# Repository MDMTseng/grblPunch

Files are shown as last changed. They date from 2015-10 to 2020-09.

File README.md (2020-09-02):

# Patch for GRBL project supporting the creation of punch machine for barrel organs.

The original GRBL Project is located at : [http://github.com/grbl/grbl](http://github.com/grbl/grbl) this project is a fork specialized in punch machines as below. It has a X and Y axis plus a punch command for punching holes in the barrel organ book.

This GRBL project has a gui for handling the punch plan, and grbl control using a PC, Mac or Linux. please see the associated software website : [www.barrel-organ-discovery.org](http://www.barrel-organ-discovery.org/site/krunch.html)

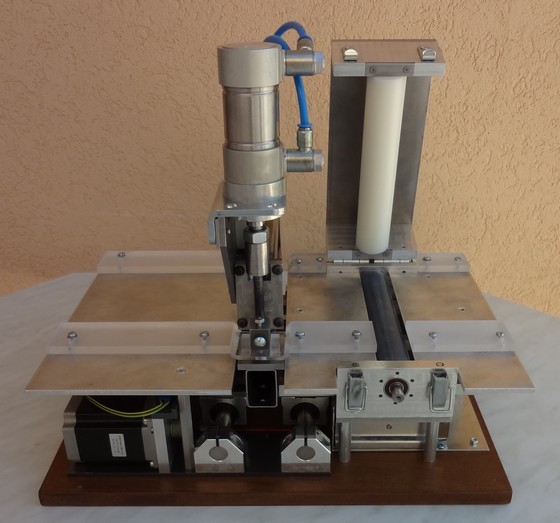
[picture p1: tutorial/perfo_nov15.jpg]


Punch machine designed and constructed by Jean Pierre Rosset.

## Introduction

This patch add a new <b>M100 GCode</b> command designed for punching machines. This new punching M100 command handle the punch cycle. This command permit to wire the punch actuators and sensor and use them in a GCode program

The punch cycle introducted is the following

- activate the punch down actuator
- wait for the punch to be on bottom (wait the activation of the punchdown sensor)
- activate the punch up actuator
- wait for the punch to be up

at least you must have two sensors for the punch positions (up and down). the activation of the up actuator is optional as some punch actuator, once desactivated, move up the punch.

Only Arduino Uno CPU is supported yet in this version.

## Grbl introducted modifications

In the adjustment of grbl software :

- The spindle is disconnected, and the pins are reuse for punching
- The D12 and D13 are now used for handling the actuators for the punch
- The A4 and A5 pins for detecting the state of the punch (up or down)

All other pins are remained the same.

## Arduino Uno connexions used by this patch

## Schematic View

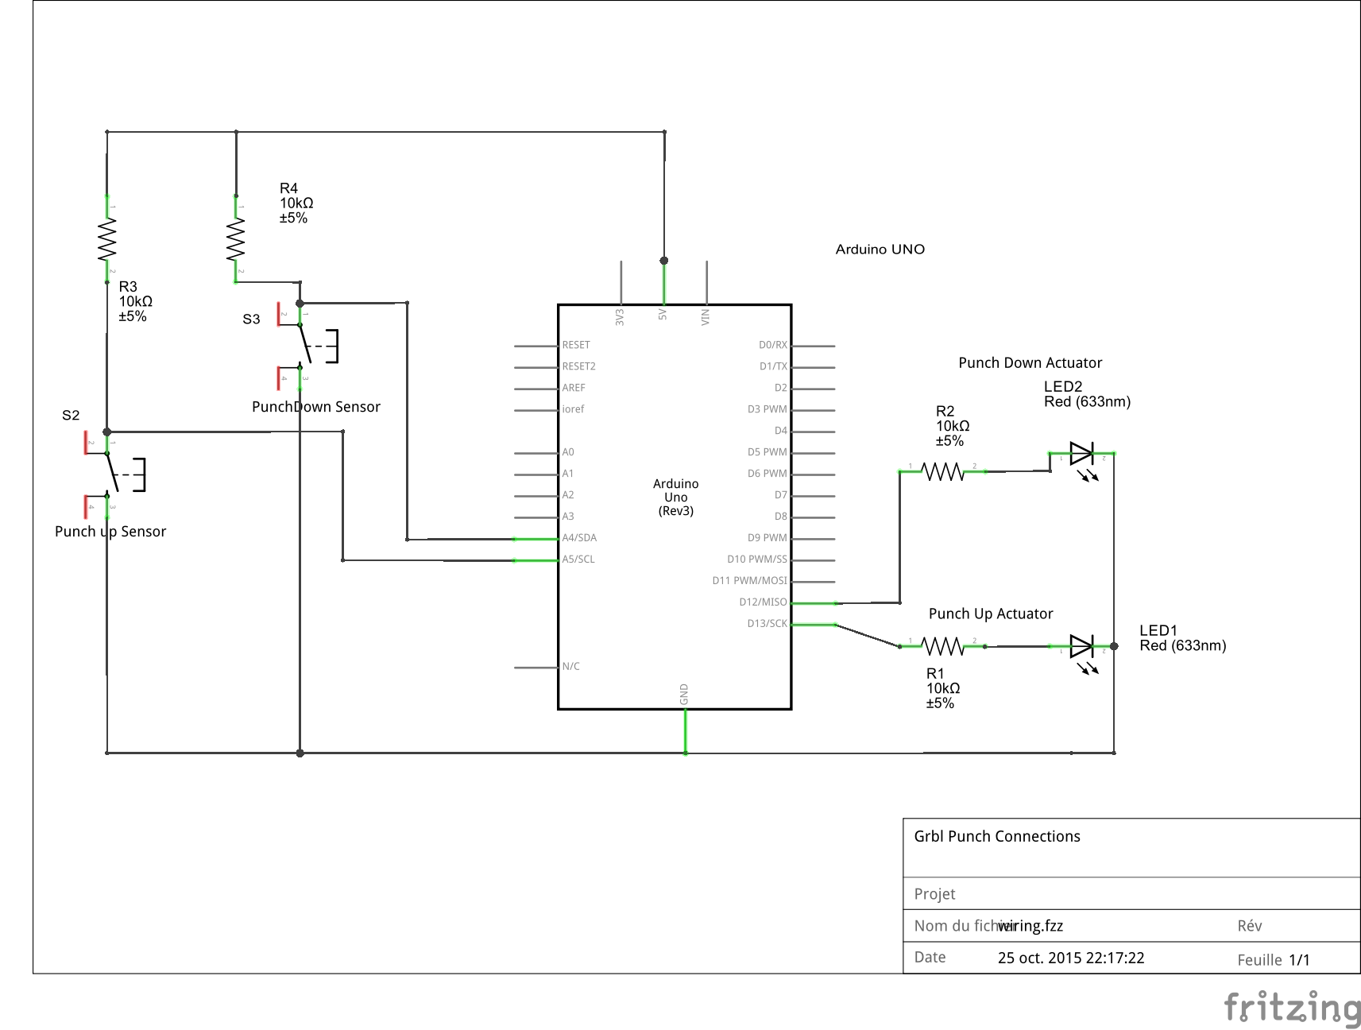
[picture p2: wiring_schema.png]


## Prototype view

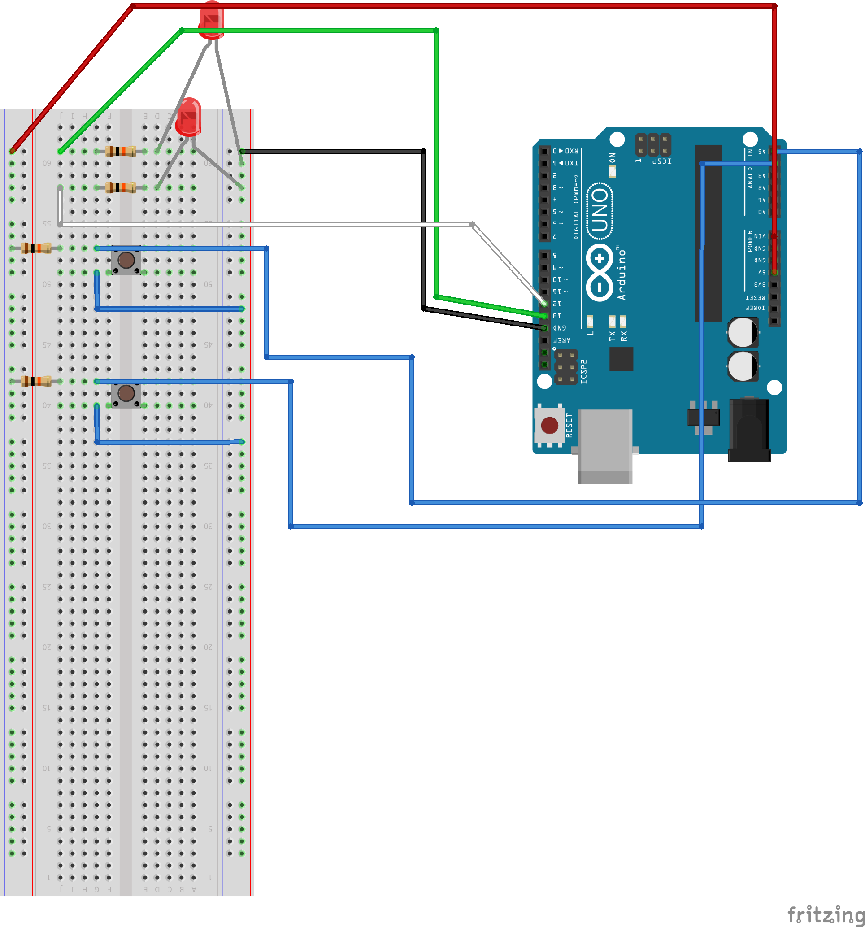
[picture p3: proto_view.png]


## Video demonstrating the new GCode Command

[https://www.youtube.com/watch?v=Sks70Pnujw8](https://www.youtube.com/watch?v=Sks70Pnujw8)

# Install the Grbl Punch software on Arduino Uno

the Easiest way to install the software is to use the XLoader software 

you can download this software at this url [http://russemotto.com/xloader/](http://russemotto.com/xloader/)

Launch XLoader

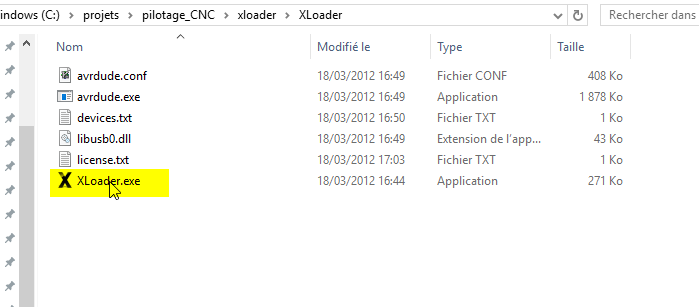
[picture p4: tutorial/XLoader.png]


Upload the grblPunch.hex file, 

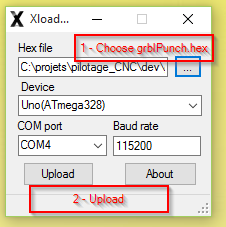
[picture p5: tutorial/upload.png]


**Warning : please download the hole project as a zip file, and take the grblPunch.hex file from it. Using internet Explorer to save the file as a text file can corrupt the file.**

That's all

You can then use the universal code sender to connect and configure the elements.

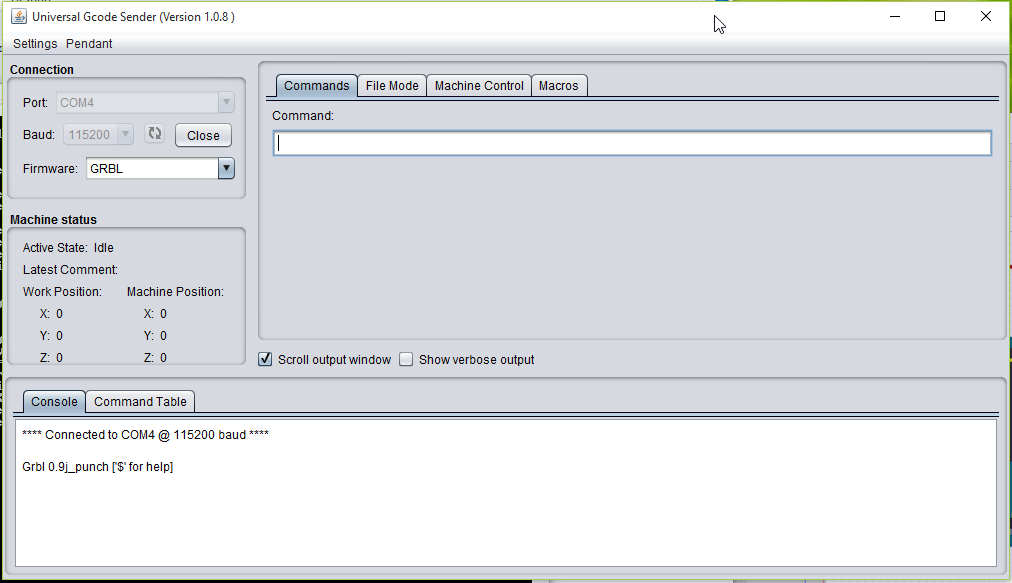
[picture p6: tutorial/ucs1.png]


## Settings 

Additional settings are introducted in this version of grbl, $30, $31, $32, $33 for adjusting the behaviour of the punch cycle, depending on the actuator and sensors used.

	>>>> $30=0 (punch actuator down invert, bool)
	>>>> $31=0 (punch actuator up invert, bool)
	>>>> $32=1 (punch sensor down invert, bool)
	>>>> $33=1 (punch sensor up invert, bool)

the $32 and $33 settings permit to invert the detection of the punch position. 

<table>
<tr>
	<th>setting</th>
	<th>value</th>
	<th>description</th>
</tr>
<tr>
	<td>$30</td>
	<td>0</td>
	<td><b>The punch down</b> actuator is activated if the PIN is at <b>"5v"</b></td>
</tr>
<tr>
	<td>$30</td>
	<td>1</td>
	<td><b>The punch down</b> actuator is activated if the PIN is at <b>"0v"</b></td>
</tr>
<tr>
	<td>$31</td>
	<td>0</td>
	<td><b>The punch up</b> actuator is activated if the PIN is at <b>"5v"</b></td>
</tr>
<tr>
	<td>$31</td>
	<td>1</td>
	<td><b>The punch up</b> actuator is activated if the PIN is at <b>"0v"</b></td>
</tr>
<tr>
	<td>$32</td>
	<td>0</td>
	<td><b>The punch down</b> is detected down if the sensor is <b>"0v"</b></td>
</tr>
<tr>
	<td>$32</td>
	<td>1</td>
	<td><b>The punch down</b> is detected down if the sensor is <b>"5v"</b></td>
</tr>
<tr>
	<td>$33</td>
	<td>0</td>
	<td><b>The punch up</b> is detected up if the sensor is <b>"0v"</b></td>
</tr>
<tr>
	<td>$33</td>
	<td>1</td>
	<td><b>The punch up</b> is detected up if the sensor is <b>"5v"</b></td>
</tr>

</table>

you can view the associated parameters in launching the $$ command

	$$
	$0=10 (step pulse, usec)
	$1=25 (step idle delay, msec)
	$2=0 (step port invert mask:00000000)
	$3=0 (dir port invert mask:00000000)
	$4=0 (step enable invert, bool)
	$5=0 (limit pins invert, bool)
	$6=0 (probe pin invert, bool)
	$10=3 (status report mask:00000011)
	$11=0.010 (junction deviation, mm)
	$12=0.002 (arc tolerance, mm)
	$13=0 (report inches, bool)
	$20=0 (soft limits, bool)
	$21=0 (hard limits, bool)
	$22=0 (homing cycle, bool)
	$23=0 (homing dir invert mask:00000000)
	$24=25.000 (homing feed, mm/min)
	$25=500.000 (homing seek, mm/min)
	$26=250 (homing debounce, msec)
	$27=1.000 (homing pull-off, mm)
	>>>> $30=0 (punch actuator down invert, bool)
	>>>> $31=0 (punch actuator up invert, bool)
	>>>> $32=0 (punch sensor down invert, bool)
	>>>> $33=0 (punch sensor up invert, bool)
	$100=250.000 (x, step/mm)
	$101=250.000 (y, step/mm)
	$102=250.000 (z, step/mm)
	$110=500.000 (x max rate, mm/min)
	$111=500.000 (y max rate, mm/min)
	$112=500.000 (z max rate, mm/min)
	$120=10.000 (x accel, mm/sec^2)
	$121=10.000 (y accel, mm/sec^2)
	$122=10.000 (z accel, mm/sec^2)
	$130=200.000 (x max travel, mm)
	$131=200.000 (y max travel, mm)
	$132=200.000 (z max travel, mm)

you can change a setting value using

	$33=1

## Improvements - RoadMap

<b>2016 - February</b>

- fix sensor detection, additional material has been setted up, we still need 2 sensors for the punch (eliminating the time in the equation)

<b>2015 - November</b>

- <strike>by settings, 
    - able to use a "pull up" logic on the hard limit
    - or use two 0-1 detector on both side of the X axis</strike>

<b>2015 - November</b>

- Validation of the master branch with a real machine

<b>Todo</b>

- Check at startup that the punch is up, before starting (part of the homing cycle checks)

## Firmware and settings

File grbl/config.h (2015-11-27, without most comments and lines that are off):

#define config_h
#include "grbl.h" // For Arduino IDE compatibility.
#define DEFAULTS_GENERIC
#define BAUD_RATE 115200
#define CPU_MAP_ATMEGA328P // Arduino Uno CPU
#define CMD_STATUS_REPORT '?'
#define CMD_FEED_HOLD '!'
#define CMD_CYCLE_START '~'
#define CMD_RESET 0x18 // ctrl-x.
#define CMD_SAFETY_DOOR '@'
#define HOMING_INIT_LOCK // Comment to disable
#define HOMING_CYCLE_0 (1<<X_AXIS)                // REQUIRED: First move Z to clear workspace.
#define N_HOMING_LOCATE_CYCLE 1 // Integer (1-128)
#define HOMING_FORCE_SET_ORIGIN // Uncomment to enable.
#define N_STARTUP_LINE 2 // Integer (1-2)
#define N_DECIMAL_COORDVALUE_INCH 4 // Coordinate or position value in inches
#define N_DECIMAL_COORDVALUE_MM   3 // Coordinate or position value in mm
#define N_DECIMAL_RATEVALUE_INCH  1 // Rate or velocity value in in/min
#define N_DECIMAL_RATEVALUE_MM    0 // Rate or velocity value in mm/min
#define N_DECIMAL_SETTINGVALUE    3 // Decimals for floating point setting values
#define MESSAGE_PROBE_COORDINATES // Enabled by default. Comment to disable.
#define SAFETY_DOOR_SPINDLE_DELAY 4000
#define SAFETY_DOOR_COOLANT_DELAY 1000
#define ACCELERATION_TICKS_PER_SECOND 100
#define ADAPTIVE_MULTI_AXIS_STEP_SMOOTHING  // Default enabled. Comment to disable.
#define TOOL_LENGTH_OFFSET_AXIS Z_AXIS // Default z-axis. Valid values are X_AXIS, Y_AXIS, or Z_AXIS.
#define PUNCH_ACTIVATED
#define MINIMUM_JUNCTION_SPEED 0.0 // (mm/min)
#define MINIMUM_FEED_RATE 1.0 // (mm/min)
#define N_ARC_CORRECTION 12 // Integer (1-255)
#define ARC_ANGULAR_TRAVEL_EPSILON 5E-7 // Float (radians)
#define DWELL_TIME_STEP 50 // Integer (1-255) (milliseconds)
#if defined(USE_SPINDLE_DIR_AS_ENABLE_PIN) && !defined(VARIABLE_SPINDLE)
  #error "USE_SPINDLE_DIR_AS_ENABLE_PIN may only be used with VARIABLE_SPINDLE enabled"
#endif
#if defined(USE_SPINDLE_DIR_AS_ENABLE_PIN) && !defined(CPU_MAP_ATMEGA328P)
  #error "USE_SPINDLE_DIR_AS_ENABLE_PIN may only be used with a 328p processor"
#endif
#if defined(VARIABLE_SPINDLE) && defined(PUNCH_ACTIVATED)
  #error "YOU CAN'T HAVE PUNCH FUNCTIONALITY WITH SPINDLE"
#endif

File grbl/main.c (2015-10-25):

/*
  main.c - An embedded CNC Controller with rs274/ngc (g-code) support
  Part of Grbl
  
  Copyright (c) 2011-2015 Sungeun K. Jeon
  Copyright (c) 2009-2011 Simen Svale Skogsrud
  
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
  You should have received a copy of the GNU General Public License
  along with Grbl.  If not, see <http://www.gnu.org/licenses/>.
*/

#include "grbl.h"


// Declare system global variable structure
system_t sys; 


int main(void)
{
  // Initialize system upon power-up.
  serial_init();   // Setup serial baud rate and interrupts
  settings_init(); // Load Grbl settings from EEPROM
  stepper_init();  // Configure stepper pins and interrupt timers
  system_init();   // Configure pinout pins and pin-change interrupt
  
  memset(&sys, 0, sizeof(sys));  // Clear all system variables
  sys.abort = true;   // Set abort to complete initialization
  sei(); // Enable interrupts

  // Check for power-up and set system alarm if homing is enabled to force homing cycle
  // by setting Grbl's alarm state. Alarm locks out all g-code commands, including the
  // startup scripts, but allows access to settings and internal commands. Only a homing
  // cycle '$H' or kill alarm locks '$X' will disable the alarm.
  // NOTE: The startup script will run after successful completion of the homing cycle, but
  // not after disabling the alarm locks. Prevents motion startup blocks from crashing into
  // things uncontrollably. Very bad.
  #ifdef HOMING_INIT_LOCK
    if (bit_istrue(settings.flags,BITFLAG_HOMING_ENABLE)) { sys.state = STATE_ALARM; }
  #endif
  
  // Force Grbl into an ALARM state upon a power-cycle or hard reset.
  #ifdef FORCE_INITIALIZATION_ALARM
    sys.state = STATE_ALARM;
  #endif
  
  // Grbl initialization loop upon power-up or a system abort. For the latter, all processes
  // will return to this loop to be cleanly re-initialized.
  for(;;) {

    // TODO: Separate configure task that require interrupts to be disabled, especially upon
    // a system abort and ensuring any active interrupts are cleanly reset.
  
    // Reset Grbl primary systems.
    serial_reset_read_buffer(); // Clear serial read buffer
    gc_init(); // Set g-code parser to default state
    spindle_init();
    punch_init();
    coolant_init();
    limits_init(); 
    probe_init();
    plan_reset(); // Clear block buffer and planner variables
    st_reset(); // Clear stepper subsystem variables.

    // Sync cleared gcode and planner positions to current system position.
    plan_sync_position();
    gc_sync_position();

    // Reset system variables.
    sys.abort = false;
    sys_rt_exec_state = 0;
    sys_rt_exec_alarm = 0;
    sys.suspend = false;
          
    // Start Grbl main loop. Processes program inputs and executes them.
    protocol_main_loop();
    
  }
  return 0;   /* Never reached */
}

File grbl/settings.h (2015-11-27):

/*
  settings.h - eeprom configuration handling 
  Part of Grbl

  Copyright (c) 2011-2015 Sungeun K. Jeon
  Copyright (c) 2009-2011 Simen Svale Skogsrud
  
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
  You should have received a copy of the GNU General Public License
  along with Grbl.  If not, see <http://www.gnu.org/licenses/>.
*/

#ifndef settings_h
#define settings_h

#include "grbl.h"


// Version of the EEPROM data. Will be used to migrate existing data from older versions of Grbl
// when firmware is upgraded. Always stored in byte 0 of eeprom
#define SETTINGS_VERSION 9  // NOTE: Check settings_reset() when moving to next version.

// Define bit flag masks for the boolean settings in settings.flag.
#define BITFLAG_REPORT_INCHES      bit(0)
// #define BITFLAG_AUTO_START         bit(1) // Obsolete. Don't alter to keep back compatibility.
#define BITFLAG_INVERT_ST_ENABLE   bit(2)
#define BITFLAG_HARD_LIMIT_ENABLE  bit(3)
#define BITFLAG_HOMING_ENABLE      bit(4)
#define BITFLAG_SOFT_LIMIT_ENABLE  bit(5)
#define BITFLAG_INVERT_LIMIT_PINS  bit(6)
#define BITFLAG_INVERT_PROBE_PIN   bit(7)

// Define status reporting boolean enable bit flags in settings.status_report_mask
#define BITFLAG_RT_STATUS_MACHINE_POSITION  bit(0)
#define BITFLAG_RT_STATUS_WORK_POSITION     bit(1)
#define BITFLAG_RT_STATUS_PLANNER_BUFFER    bit(2)
#define BITFLAG_RT_STATUS_SERIAL_RX         bit(3)
#define BITFLAG_RT_STATUS_LIMIT_PINS        bit(4)

// Define settings restore bitflags.
#define SETTINGS_RESTORE_ALL 0xFF // All bitflags
#define SETTINGS_RESTORE_DEFAULTS bit(0)
#define SETTINGS_RESTORE_PARAMETERS bit(1)
#define SETTINGS_RESTORE_STARTUP_LINES bit(2)
#define SETTINGS_RESTORE_BUILD_INFO bit(3)

// Define EEPROM memory address location values for Grbl settings and parameters
// NOTE: The Atmega328p has 1KB EEPROM. The upper half is reserved for parameters and
// the startup script. The lower half contains the global settings and space for future 
// developments.
#define EEPROM_ADDR_GLOBAL         1U
#define EEPROM_ADDR_PARAMETERS     512U
#define EEPROM_ADDR_STARTUP_BLOCK  768U
#define EEPROM_ADDR_BUILD_INFO     942U

// Define EEPROM address indexing for coordinate parameters
#define N_COORDINATE_SYSTEM 6  // Number of supported work coordinate systems (from index 1)
#define SETTING_INDEX_NCOORD N_COORDINATE_SYSTEM+1 // Total number of system stored (from index 0)
// NOTE: Work coordinate indices are (0=G54, 1=G55, ... , 6=G59)
#define SETTING_INDEX_G28    N_COORDINATE_SYSTEM    // Home position 1
#define SETTING_INDEX_G30    N_COORDINATE_SYSTEM+1  // Home position 2
// #define SETTING_INDEX_G92    N_COORDINATE_SYSTEM+2  // Coordinate offset (G92.2,G92.3 not supported)

// Define Grbl axis settings numbering scheme. Starts at START_VAL, every INCREMENT, over N_SETTINGS.
#define AXIS_N_SETTINGS          4
#define AXIS_SETTINGS_START_VAL  100 // NOTE: Reserving settings values >= 100 for axis settings. Up to 255.
#define AXIS_SETTINGS_INCREMENT  10  // Must be greater than the number of axis settings


// GRBL Punch parameters
//
#define DEFAULT_PUNCH_ACTUATOR_INVERT_MASK 0
#define DEFAULT_PUNCH_SENSOR_INVERT_MASK 0

#define BITFLAG_PUNCH_ACTUATOR_UP bit(0)
#define BITFLAG_PUNCH_ACTUATOR_DOWN bit(1)

#define BITFLAG_PUNCH_SENSOR_UP bit(0)
#define BITFLAG_PUNCH_SENSOR_DOWN bit(1)

// Global persistent settings (Stored from byte EEPROM_ADDR_GLOBAL onwards)
typedef struct {
  // Axis settings
  float steps_per_mm[N_AXIS];
  float max_rate[N_AXIS];
  float acceleration[N_AXIS];
  float max_travel[N_AXIS];

  // Remaining Grbl settings
  uint8_t pulse_microseconds;
  uint8_t step_invert_mask;
  uint8_t dir_invert_mask;
  uint8_t stepper_idle_lock_time; // If max value 255, steppers do not disable.
  uint8_t status_report_mask; // Mask to indicate desired report data.
  float junction_deviation;
  float arc_tolerance;
  
  uint8_t flags;  // Contains default boolean settings

  uint8_t homing_dir_mask;
  float homing_feed_rate;
  float homing_seek_rate;
  uint16_t homing_debounce_delay;
  float homing_pulloff;

  // grblPunch settings
  uint8_t punch_actuator_invert_mask;
  uint8_t punch_sensor_invert_mask;

} settings_t;
extern settings_t settings;

// Initialize the configuration subsystem (load settings from EEPROM)
void settings_init();

// Helper function to clear and restore EEPROM defaults
void settings_restore(uint8_t restore_flag);

// A helper method to set new settings from command line
uint8_t settings_store_global_setting(uint8_t parameter, float value);

// Stores the protocol line variable as a startup line in EEPROM
void settings_store_startup_line(uint8_t n, char *line);

// Reads an EEPROM startup line to the protocol line variable
uint8_t settings_read_startup_line(uint8_t n, char *line);

// Stores build info user-defined string
void settings_store_build_info(char *line);

// Reads build info user-defined string
uint8_t settings_read_build_info(char *line);

// Writes selected coordinate data to EEPROM
void settings_write_coord_data(uint8_t coord_select, float *coord_data);

// Reads selected coordinate data from EEPROM
uint8_t settings_read_coord_data(uint8_t coord_select, float *coord_data);

// Returns the step pin mask according to Grbl's internal axis numbering
uint8_t get_step_pin_mask(uint8_t i);

// Returns the direction pin mask according to Grbl's internal axis numbering
uint8_t get_direction_pin_mask(uint8_t i);

// Returns the limit pin mask according to Grbl's internal axis numbering
uint8_t get_limit_pin_mask(uint8_t i);


#endif

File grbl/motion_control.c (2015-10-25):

/*
  motion_control.c - high level interface for issuing motion commands
  Part of Grbl

  Copyright (c) 2011-2015 Sungeun K. Jeon
  Copyright (c) 2009-2011 Simen Svale Skogsrud
  Copyright (c) 2011 Simen Svale Skogsrud
  
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
  You should have received a copy of the GNU General Public License
  along with Grbl.  If not, see <http://www.gnu.org/licenses/>.
*/

#include "grbl.h"


// Execute linear motion in absolute millimeter coordinates. Feed rate given in millimeters/second
// unless invert_feed_rate is true. Then the feed_rate means that the motion should be completed in
// (1 minute)/feed_rate time.
// NOTE: This is the primary gateway to the grbl planner. All line motions, including arc line 
// segments, must pass through this routine before being passed to the planner. The seperation of
// mc_line and plan_buffer_line is done primarily to place non-planner-type functions from being
// in the planner and to let backlash compensation or canned cycle integration simple and direct.
#ifdef USE_LINE_NUMBERS
  void mc_line(float *target, float feed_rate, uint8_t invert_feed_rate, int32_t line_number)
#else
  void mc_line(float *target, float feed_rate, uint8_t invert_feed_rate)
#endif
{
  // If enabled, check for soft limit violations. Placed here all line motions are picked up
  // from everywhere in Grbl.
  if (bit_istrue(settings.flags,BITFLAG_SOFT_LIMIT_ENABLE)) { limits_soft_check(target); }    
      
  // If in check gcode mode, prevent motion by blocking planner. Soft limits still work.
  if (sys.state == STATE_CHECK_MODE) { return; }
    
  // NOTE: Backlash compensation may be installed here. It will need direction info to track when
  // to insert a backlash line motion(s) before the intended line motion and will require its own
  // plan_check_full_buffer() and check for system abort loop. Also for position reporting 
  // backlash steps will need to be also tracked, which will need to be kept at a system level.
  // There are likely some other things that will need to be tracked as well. However, we feel
  // that backlash compensation should NOT be handled by Grbl itself, because there are a myriad
  // of ways to implement it and can be effective or ineffective for different CNC machines. This
  // would be better handled by the interface as a post-processor task, where the original g-code
  // is translated and inserts backlash motions that best suits the machine. 
  // NOTE: Perhaps as a middle-ground, all that needs to be sent is a flag or special command that
  // indicates to Grbl what is a backlash compensation motion, so that Grbl executes the move but
  // doesn't update the machine position values. Since the position values used by the g-code
  // parser and planner are separate from the system machine positions, this is doable.

  // If the buffer is full: good! That means we are well ahead of the robot. 
  // Remain in this loop until there is room in the buffer.
  do {
    protocol_execute_realtime(); // Check for any run-time commands
    if (sys.abort) { return; } // Bail, if system abort.
    if ( plan_check_full_buffer() ) { protocol_auto_cycle_start(); } // Auto-cycle start when buffer is full.
    else { break; }
  } while (1);

  // Plan and queue motion into planner buffer
  #ifdef USE_LINE_NUMBERS
    plan_buffer_line(target, feed_rate, invert_feed_rate, line_number);
  #else
    plan_buffer_line(target, feed_rate, invert_feed_rate);
  #endif
}


// Execute an arc in offset mode format. position == current xyz, target == target xyz, 
// offset == offset from current xyz, axis_X defines circle plane in tool space, axis_linear is
// the direction of helical travel, radius == circle radius, isclockwise boolean. Used
// for vector transformation direction.
// The arc is approximated by generating a huge number of tiny, linear segments. The chordal tolerance
// of each segment is configured in settings.arc_tolerance, which is defined to be the maximum normal
// distance from segment to the circle when the end points both lie on the circle.
#ifdef USE_LINE_NUMBERS
  void mc_arc(float *position, float *target, float *offset, float radius, float feed_rate, 
    uint8_t invert_feed_rate, uint8_t axis_0, uint8_t axis_1, uint8_t axis_linear, uint8_t is_clockwise_arc, int32_t line_number)
#else
  void mc_arc(float *position, float *target, float *offset, float radius, float feed_rate,
    uint8_t invert_feed_rate, uint8_t axis_0, uint8_t axis_1, uint8_t axis_linear, uint8_t is_clockwise_arc)
#endif
{
  float center_axis0 = position[axis_0] + offset[axis_0];
  float center_axis1 = position[axis_1] + offset[axis_1];
  float r_axis0 = -offset[axis_0];  // Radius vector from center to current location
  float r_axis1 = -offset[axis_1];
  float rt_axis0 = target[axis_0] - center_axis0;
  float rt_axis1 = target[axis_1] - center_axis1;
  
  // CCW angle between position and target from circle center. Only one atan2() trig computation required.
  float angular_travel = atan2(r_axis0*rt_axis1-r_axis1*rt_axis0, r_axis0*rt_axis0+r_axis1*rt_axis1);
  if (is_clockwise_arc) { // Correct atan2 output per direction
    if (angular_travel >= -ARC_ANGULAR_TRAVEL_EPSILON) { angular_travel -= 2*M_PI; }
  } else {
    if (angular_travel <= ARC_ANGULAR_TRAVEL_EPSILON) { angular_travel += 2*M_PI; }
  }

  // NOTE: Segment end points are on the arc, which can lead to the arc diameter being smaller by up to
  // (2x) settings.arc_tolerance. For 99% of users, this is just fine. If a different arc segment fit
  // is desired, i.e. least-squares, midpoint on arc, just change the mm_per_arc_segment calculation.
  // For the intended uses of Grbl, this value shouldn't exceed 2000 for the strictest of cases.
  uint16_t segments = floor(fabs(0.5*angular_travel*radius)/
                          sqrt(settings.arc_tolerance*(2*radius - settings.arc_tolerance)) );
  
  if (segments) { 
    // Multiply inverse feed_rate to compensate for the fact that this movement is approximated
    // by a number of discrete segments. The inverse feed_rate should be correct for the sum of 
    // all segments.
    if (invert_feed_rate) { feed_rate *= segments; }
   
    float theta_per_segment = angular_travel/segments;
    float linear_per_segment = (target[axis_linear] - position[axis_linear])/segments;
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

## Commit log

2015-10-25 add code + documentation
    [config.h, wiring.fzz]
2015-11-15 fix synchro M100
    [config.h, wiring.fzz]
2015-11-19 rename the grbl.hex to grblPunch.hex
2016-02-07 fix sensor inversion
    [wiring.fzz]
2016-02-07 revert pin4 and 5
    [cpu_map_atmega328p.h]
2016-02-07 documentation update associated to pin4 - pin5 invert
    [wiring.fzz]
2016-02-07 add warning when using internet explorer for grblpunch.hex file

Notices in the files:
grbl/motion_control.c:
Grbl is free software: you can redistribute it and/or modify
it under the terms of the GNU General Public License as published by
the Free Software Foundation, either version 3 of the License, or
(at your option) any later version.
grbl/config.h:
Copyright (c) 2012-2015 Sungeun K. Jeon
